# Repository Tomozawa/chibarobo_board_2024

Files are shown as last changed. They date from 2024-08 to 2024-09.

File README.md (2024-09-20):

# chiba_robo_board_2024
## 概要
ちばロボ2024に参加する1年生向けの制御基板です。

## 機能一覧
- マイコンボードESP32S2-DevKitM-1で操作可能
- Cytron MD10C向けコントロールピンx5
- 60kgサーボ向けコントロールピン&amp;7.5V/5A高効率電源
- マイコンボード直結GPIOピン
- 12~24VDC/50Aのアクチュエータ電源
- 外付け非常停止スイッチ
- ソフトスタート内蔵

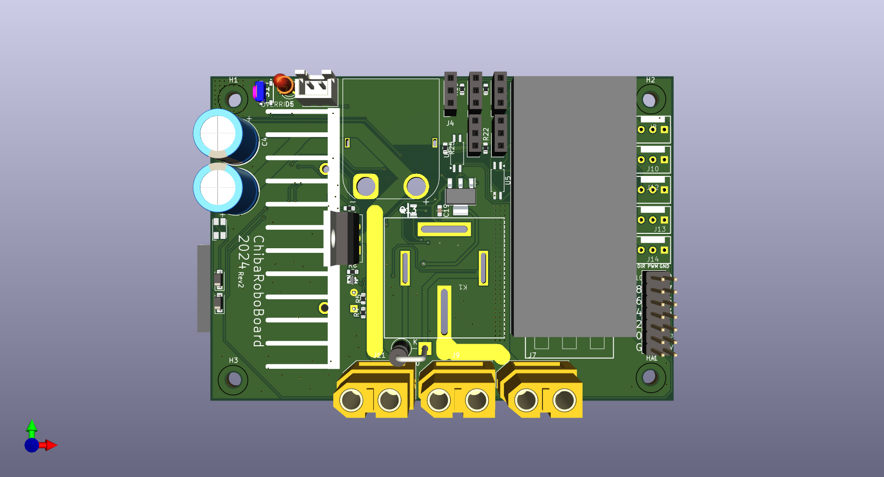
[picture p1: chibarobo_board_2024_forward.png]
chibarobo_board_2024_forward

<br>前面

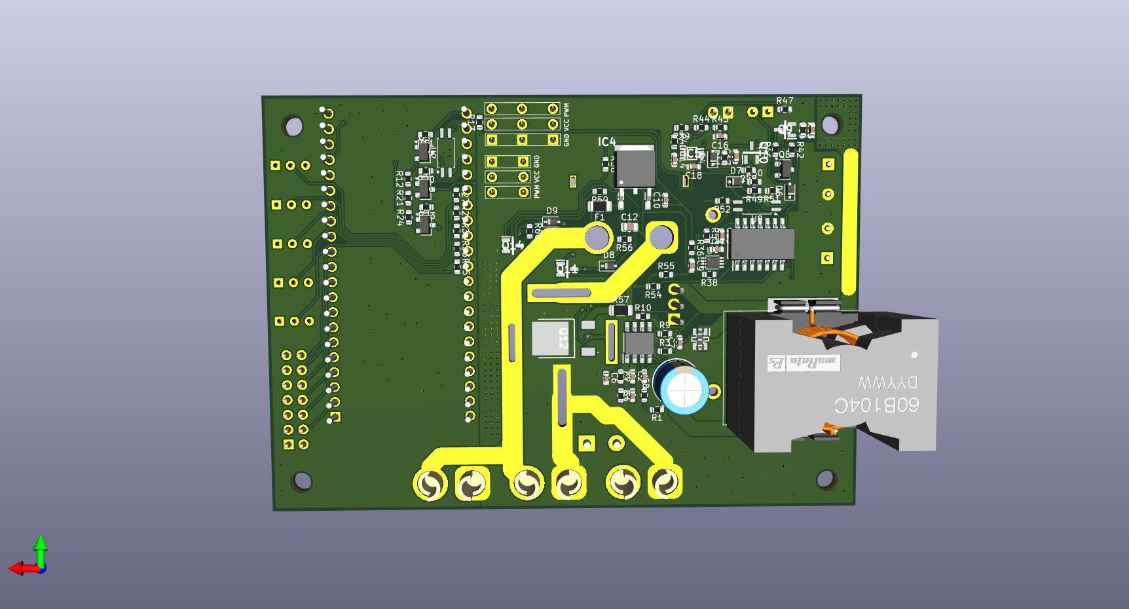
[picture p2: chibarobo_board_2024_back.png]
chibarobo_board_2024_back

<br>背面

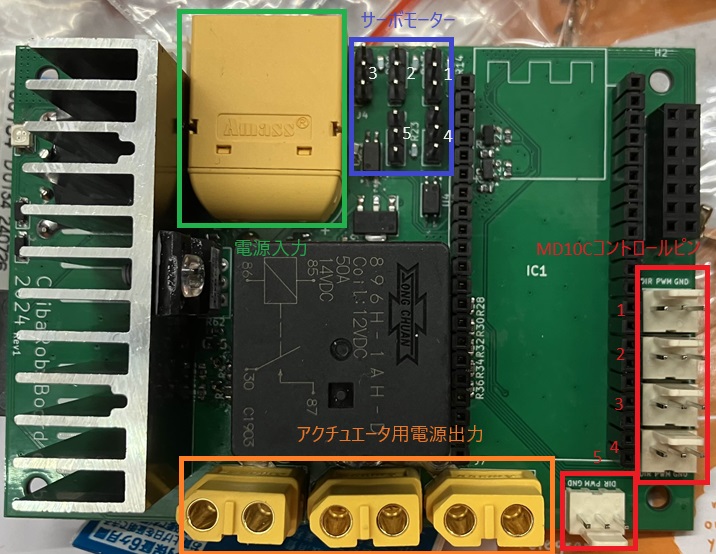
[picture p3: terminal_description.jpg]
terminal_descrition


# マイコンボード
本基板はESP32S2-DevKitM-1でアクチュエータ類を操作します。基板上のピンソケットに、シルクに描画されている向きに従ってESP32S2-DevKitM-1を差し込んでください。

各種アクチュエータ/センサとマイコンボードのピンアサインは以下のとおりです。
| ピン | アクチュエータ/センサ | 説明 |
| ----- | ----- | --- |
| 33 | DCモーター1 | DCモーター1のPWM信号 |
| 34 | DCモーター2 | DCモーター2のPWM信号 |
| 35 | DCモーター3 | DCモーター3のPWM信号 |
| 36 | DCモーター4 | DCモーター4のPWM信号 |
| 37 | DCモーター5 | DCモーター5のPWM信号 |
| 38 | DCモーター1 | DCモーター1のDIR信号 |
| 39 | DCモーター2 | DCモーター2のDIR信号 |
| 40 | DCモーター3 | DCモーター3のDIR信号 |
| 41 | DCモーター4 | DCモーター4のDIR信号 |
| 42 | DCモーター5 | DCモーター5のDIR信号 |
| 18 | サーボモーター1 | サーボモーター1のPWM信号 |
| 19 | サーボモーター2 | サーボモーター2のPWM信号 |
| 20 | サーボモーター3 | サーボモーター3のPWM信号 |
| 21 | サーボモーター4 | サーボモーター4のPWM信号 |
| 26 | サーボモーター5 | サーボモーター5のPWM信号 |
| 16 | 非常停止ボタン | HIGH: 非常停止ボタンが押されて**いない** LOW:非常停止ボタンが押されて**いる** |
| 5V || ロジック電源で動く回路の電源 |
| GND || ロジック電源で動く回路の共通電位 |

16番ピンは、出力モードに**設定しない**でください。非常停止ボタンのオーバーライド機能が無効になったり、非常停止ボタンが扱われた際、リレーが遮断しなくなることがあります。

# Cytron MD10C向けコントロールピン
Cytron製モータードライバ「Cytron MD10C」向けのDIR/PWM/GNDピンを5チャンネル提供します。

DIRピンのHigh/Low切り替えにより、回転方向を変化させます。

PWMピンから出力するPWM信号のデューティー比により、回転速度を変化させます。

GNDピンの電位は、マイコンボードのGNDピンと同電位です。

DIR/PWMピンの出力インピーダンスは2.2kOhm、ロジック電圧は3.3Vです。

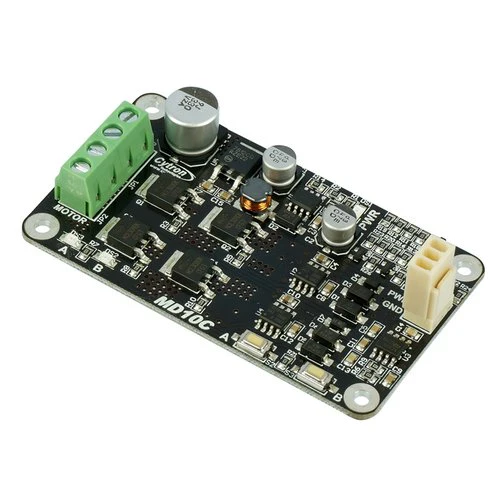
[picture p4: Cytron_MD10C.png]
Cytron MD10C


# サーボモーター電源/コントロールピン
60kgサーボ向けの7.5V/5A電源および、マイコンボードと絶縁されたPWM信号を提供します。

基板上のピンヘッダに、サーボモーターのQIコネクタを接続するだけで使用できます。

最大5個まで接続可能です(最小動作電流1Aの場合)。

> [!WARNING]
> - 3.3Vや5Vで動作するサーボモーターを接続しないでください。サーボモーターが焼損する可能性があります。
> - DCDCコンバータICの電流制限機能を外しています。出力電流の管理は、使用者の責任です(<span style="color: red;">最大5Aまで<span>)。

> [!NOTE]
> 無負荷時に150mA程度消費しますが、同期型DCDCコンバータの特性であり、故障ではありません。

# マイコンボード直結のGPIOピン
その他のアクチュエータおよびセンサを接続可能なGPIOピンを備えています。また、特定のGPIOピンからは、EMS信号(非常停止ボタンの信号)を取り出すことができます。(EMS信号を除き)出力電圧/電流は、ESP32S2-DevKitM-1の駆動能力に依存します。すなわち、3.3V/&pm;15mAの駆動能力を持ちます。

EMS信号は3.3V出力で、2.2kOhmの出力インピーダンスを持ちます。

# 12~24VDC/50Aのアクチュエータ電源
アクチュエータの動作に必要な電源を供給するための、電源ハブ機能を備えています。12~24VDC/50Aの範囲の直流電流を流すことができます。

# 外付け非常停止スイッチ
外付けの非常停止スイッチ(NO接点)を使うことで、非常時にアクチュエータ電源を遮断します。また、非常停止スイッチが扱われた際は、マイコンボードに信号が送られます。

外付け非常停止スイッチを使用しない場合、OVERRIDEボタンを使用することで、非常停止機能を一時的に無効にできます。

# ソフトスタート内蔵
バッテリーや端子への負荷を軽減するため、簡易的なソフトスタート機能を備えています。この機能は、電源投入から100ms間、アクチュエータ電源の消費電流を500mAに制限します。これは、アクチュエータ電源に2000uFまでの容量性負荷を接続することを可能にします。

# 確認されているバグ
- LEDのフットプリントミス(D0603サイズ(:サークル標準サイズ)のチップLEDを2つつけることで対処可能)

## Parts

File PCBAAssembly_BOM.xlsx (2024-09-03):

Designator | Comment | Footprint | JLCPCB Parts#
C1 | 8.2n | Capacitor_SMD:C_0603_1608Metric
C2 | 18p | Capacitor_SMD:C_0603_1608Metric
C3 | 3.3n | Capacitor_SMD:C_0603_1608Metric
C6 | 100n | Capacitor_SMD:C_0603_1608Metric
C7 | 100n | Capacitor_SMD:C_0603_1608Metric
C9 | 1u | Capacitor_SMD:C_0603_1608Metric
C10 | 100n | Capacitor_SMD:C_0603_1608Metric
C11 | 100n | Capacitor_SMD:C_0603_1608Metric
C12 | 10u | Capacitor_SMD:C_0805_2012Metric
C13 | 100n | Capacitor_SMD:C_0603_1608Metric
C14 | 100n | Capacitor_SMD:C_0603_1608Metric
C15 | 1u | Capacitor_SMD:C_0603_1608Metric
C16 | 100n | Capacitor_SMD:C_0603_1608Metric
C17 | 100n | Capacitor_SMD:C_0603_1608Metric
C18 | 100n | Capacitor_SMD:C_0603_1608Metric
D4 | D_Schottky | Diode_SMD:D_SOD-323F | C50704
D6 | D_Schottky | Diode_SMD:D_SOD-323F | C50704
D7 | D_Schottky | Diode_SMD:D_SOD-323F | C50704
D8 | 12V_Zener | Diode_SMD:D_SOD-323 | C19077447
D9 | 12V_Zener | Diode_SMD:D_SOD-323 | C19077447
IC4 | L78M05CDT | SamacSys_Parts:TO225P972X240-3N | C55509
Q3 | 2SA1162-GR_F_ | Package_TO_SOT_SMD:SC-59 | C155455
Q6 | 2SA1162-GR_F_ | Package_TO_SOT_SMD:SC-59 | C155455
Q7 | 2SA1162-GR_F_ | Package_TO_SOT_SMD:SC-59 | C155455
Q8 | 2SA1162-GR_F_ | Package_TO_SOT_SMD:SC-59 | C155455
Q9 | 2SC2712-GR_TE85L,F | SamacSys_Parts:SOT95P260X156-3N | C83447
Q10 | 2SC2712-GR_TE85L,F | SamacSys_Parts:SOT95P260X156-3N | C83447
Q11 | 2SC2712-GR_TE85L,F | SamacSys_Parts:SOT95P260X156-3N | C83447
Q14 | 2SC2712-GR_TE85L,F | SamacSys_Parts:SOT95P260X156-3N | C83447
R1 | 330 | Resistor_SMD:R_0603_1608Metric
R2 | 18 | Resistor_SMD:R_0603_1608Metric
R3 | 1.6k | Resistor_SMD:R_0603_1608Metric
R6 | 3k | Resistor_SMD:R_0603_1608Metric
R7 | 56k | Resistor_SMD:R_0603_1608Metric
R9 | 56k | Resistor_SMD:R_0603_1608Metric
R10 | 1k | Resistor_SMD:R_0603_1608Metric
R11 | 16k | Resistor_SMD:R_0603_1608Metric
R12 | 330 | Resistor_SMD:R_0603_1608Metric
R13 | 560 | Resistor_SMD:R_0603_1608Metric
R20 | 16k | Resistor_SMD:R_0603_1608Metric
R21 | 330 | Resistor_SMD:R_0603_1608Metric
R23 | 16k | Resistor_SMD:R_0603_1608Metric
R24 | 330 | Resistor_SMD:R_0603_1608Metric
R27 | 2.2k | Resistor_SMD:R_0603_1608Metric
R29 | 2.2k | Resistor_SMD:R_0603_1608Metric
R31 | 2.2k | Resistor_SMD:R_0603_1608Metric
R33 | 2.2k | Resistor_SMD:R_0603_1608Metric
R35 | 2.2k | Resistor_SMD:R_0603_1608Metric
R36 | 200k | Resistor_SMD:R_0603_1608Metric
R38 | 2.2k | Resistor_SMD:R_0603_1608Metric
R39 | 2.2k | Resistor_SMD:R_0603_1608Metric
R40 | 100k | Resistor_SMD:R_0603_1608Metric
R41 | 470 | Resistor_SMD:R_0603_1608Metric
R42 | 470 | Resistor_SMD:R_0603_1608Metric
R43 | 100 | Resistor_SMD:R_0603_1608Metric
R44 | 2.2k | Resistor_SMD:R_0603_1608Metric
R45 | 100k | Resistor_SMD:R_0603_1608Metric
R46 | 430 | Resistor_SMD:R_0603_1608Metric
R47 | 390 | Resistor_SMD:R_0603_1608Metric
R48 | 4.3k | Resistor_SMD:R_0603_1608Metric
R49 | 1.2k | Resistor_SMD:R_0603_1608Metric
R50 | 3.3k | Resistor_SMD:R_0603_1608Metric
R51 | 360 | Resistor_SMD:R_0603_1608Metric
R52 | 10k | Resistor_SMD:R_0603_1608Metric
R53 | 2.2k | Resistor_SMD:R_0603_1608Metric
R54 | 5.6k | Resistor_SMD:R_0603_1608Metric
R55 | 1k | Resistor_SMD:R_0603_1608Metric
R56 | 2.2k | Resistor_SMD:R_0603_1608Metric
R58 | 10k | Resistor_SMD:R_0603_1608Metric
R59 | 1.3k | Resistor_SMD:R_0603_1608Metric
R60 | 300 | Resistor_SMD:R_0603_1608Metric
U2 | TLP291 | Package_SO:SOIC-4_4.55x2.6mm_P1.27mm | C5121290
U7 | 74LVC1G123 | Package_SO:VSSOP-8_2.3x2mm_P0.5mm | C77273
U8 | TLP291 | Package_SO:SOIC-4_4.55x2.6mm_P1.27mm | C5121290

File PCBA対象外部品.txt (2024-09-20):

C4, C5, C19, C8, C19, D1, D2, D3, D5, D10, F1, HS1, IC1, IC2, IC3, IC5, J1, J8, J10, J12, J13, J14, K1, L1, Q1, Q12, Q13, Q15, Q2, Q4, Q5, R14, R15, R16, R17, R18, R19, R22, R25, R26, R28, R30, R32, R34, R37, R4, R5, R57, R8, S1, U1, U3, U4, U5, U6

所有(新品)
C4, C5, C19, F1, IC1, J8, J10, J12, J13, J14(1つのみ), K1, R28, R30, R32, R34, R37, R4, R5, S1

所有(部品取り)
D1(1つのみ), D2(1つのみ),D3(1つのみ), HS1(1つのみ), IC2(1つのみ), J8(1つのみ), J10(1つのみ), J12(1つのみ), J13(1つのみ), J14(1つのみ), L1(1つのみ), Q12(1つのみ), Q13, Q15(1つのみ), Q2(1つのみ), Q4, Q5, R57, R14, R15, R16, R17, R18, R19, R22, R25, R8, U3, U4, U5, U6

要購入
C8, D1(1つのみ), D2(1つのみ), D3(1つのみ), D5, D10, HS1(1つのみ), IC2(1つのみ), IC3, IC5, J1, L1(1つのみ), Q1, Q12(1つのみ), Q15(1つのみ), Q2(1つのみ), R57, U1

マルツ
D1(1つのみ), D2(1つのみ), D3(1つのみ), IC2(1つのみ), IC3, IC5, L1(1つのみ), Q1, Q12(1つのみ), Q15(1つのみ), Q2(1つのみ), R57, U1

秋月
C8, D10, J1

千石
D5, HS1(1つのみ),

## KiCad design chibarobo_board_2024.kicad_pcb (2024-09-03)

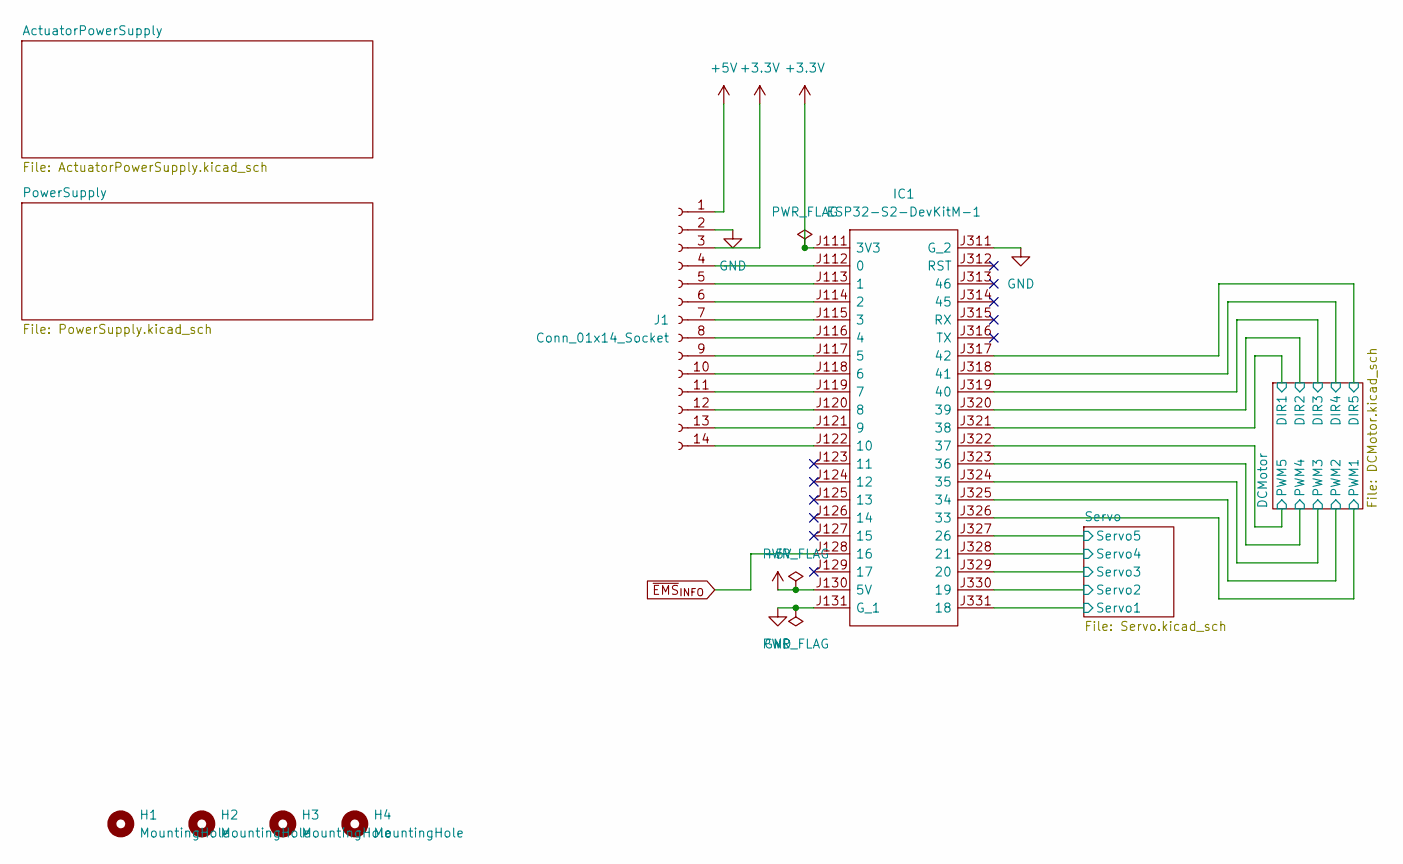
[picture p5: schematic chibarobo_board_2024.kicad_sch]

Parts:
H1, H2, H3, H4: MountingHole; MountingHole_3.2mm_M3
IC1: ESP32-S2-DevKitM-1; ESP32S2DevKitM1; Manufacturer_Part_Number ESP32-S2-DevKitM-1; Mouser Part Number 356-ESP32-S2DEVKITM1
J1: Conn_01x14_Socket; PinHeader_2x07_P2.54mm_Vertical

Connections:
+3.3V: IC1.J111 (3V3), J1.3
+5V: IC1.J130 (5V), J1.1; also elsewhere on the board
/DCMotor/DIR1: IC1.J321 (38); also elsewhere on the board
/DCMotor/DIR2: IC1.J320 (39); also elsewhere on the board
/DCMotor/DIR3: IC1.J319 (40); also elsewhere on the board
/DCMotor/DIR4: IC1.J318 (41); also elsewhere on the board
/DCMotor/DIR5: IC1.J317 (42); also elsewhere on the board
/DCMotor/PWM1: IC1.J326 (33); also elsewhere on the board
/DCMotor/PWM2: IC1.J325 (34); also elsewhere on the board
/DCMotor/PWM3: IC1.J324 (35); also elsewhere on the board
/DCMotor/PWM4: IC1.J323 (36); also elsewhere on the board
/DCMotor/PWM5: IC1.J322 (37); also elsewhere on the board
/Servo/Servo1: IC1.J331 (18); also elsewhere on the board
/Servo/Servo2: IC1.J330 (19); also elsewhere on the board
/Servo/Servo3: IC1.J329 (20); also elsewhere on the board
/Servo/Servo4: IC1.J328 (21); also elsewhere on the board
/Servo/Servo5: IC1.J327 (26); also elsewhere on the board
GND: IC1.J131 (G_1), IC1.J311 (G_2), J1.2; also elsewhere on the board
unnamed: IC1.J112 (0), J1.4
unnamed: IC1.J113 (1), J1.5
unnamed: IC1.J114 (2), J1.6
unnamed: IC1.J115 (3), J1.7
unnamed: IC1.J116 (4), J1.8
unnamed: IC1.J117 (5), J1.9
unnamed: IC1.J118 (6), J1.10
unnamed: IC1.J119 (7), J1.11
unnamed: IC1.J120 (8), J1.12
unnamed: IC1.J121 (9), J1.13
unnamed: IC1.J122 (10), J1.14
~EMS_{INFO}: IC1.J128 (16); also elsewhere on the board

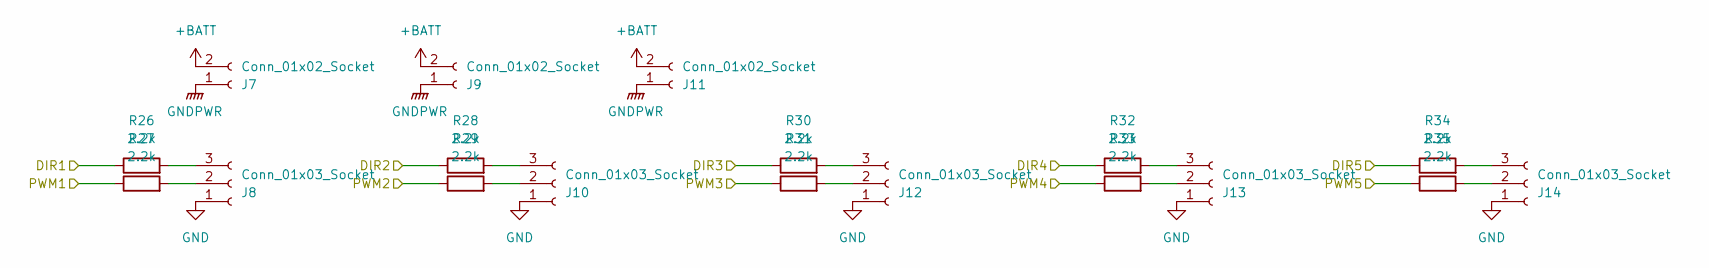
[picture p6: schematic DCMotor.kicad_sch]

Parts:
J7, J9, J11: Conn_01x02_Socket; AMASS_XT60-F_1x02_P7.20mm_Vertical
J8, J10, J12, J13, J14: Conn_01x03_Socket; Connector_2510-3P
R26, R27, R28, R29, R30, R31, R32, R33, R34, R35: 2.2k; R_0603_1608Metric

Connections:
+BATT: J7.2, J9.2, J11.2; also elsewhere on the board
/DCMotor/DIR1: R26.1; also elsewhere on the board
/DCMotor/DIR2: R28.1; also elsewhere on the board
/DCMotor/DIR3: R30.1; also elsewhere on the board
/DCMotor/DIR4: R32.1; also elsewhere on the board
/DCMotor/DIR5: R34.1; also elsewhere on the board
/DCMotor/PWM1: R27.1; also elsewhere on the board
/DCMotor/PWM2: R29.1; also elsewhere on the board
/DCMotor/PWM3: R31.1; also elsewhere on the board
/DCMotor/PWM4: R33.1; also elsewhere on the board
/DCMotor/PWM5: R35.1; also elsewhere on the board
GND: J8.1, J10.1, J12.1, J13.1, J14.1; also elsewhere on the board
GNDPWR: J7.1, J9.1, J11.1; also elsewhere on the board
unnamed: J8.2, R27.2
unnamed: J8.3, R26.2
unnamed: J10.2, R29.2
unnamed: J10.3, R28.2
unnamed: J12.2, R31.2
unnamed: J12.3, R30.2
unnamed: J13.2, R33.2
unnamed: J13.3, R32.2
unnamed: J14.2, R35.2
unnamed: J14.3, R34.2

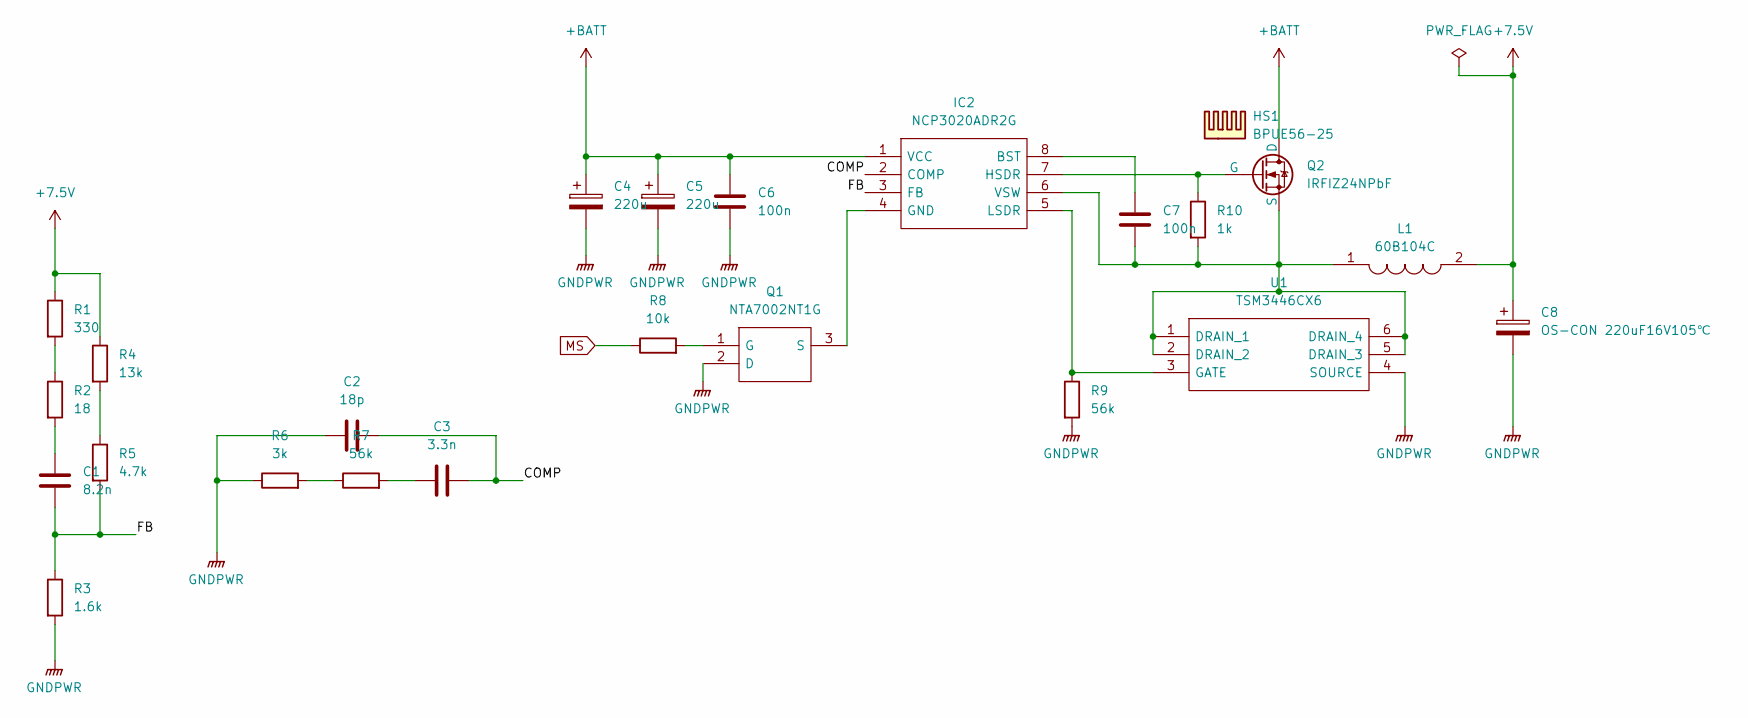
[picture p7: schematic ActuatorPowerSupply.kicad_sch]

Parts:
C1: 8.2n; C_0603_1608Metric
C2: 18p; C_0603_1608Metric
C3: 3.3n; C_0603_1608Metric
C4, C5: 220u; CP_Radial_D10.0mm_P5.00mm
C6, C7: 100n; C_0603_1608Metric
C8: OS-CON 220uF16V105℃; CP_Radial_D8.0mm_P3.50mm
HS1: BPUE56-25; BPUE56
IC2: NCP3020ADR2G; SOIC127P600X175-8N; Manufacturer_Part_Number NCP3020ADR2G; Mouser Part Number 863-NCP3020ADR2G
L1: 60B104C; 60B104C_correct; Manufacturer_Part_Number 60B104C; Mouser Part Number 580-60B104C
Q1: NTA7002NT1G; SOT50P160X90-3N; Manufacturer_Part_Number NTA7002NT1G; Mouser Part Number 863-NTA7002NT1G
Q2: IRFIZ24NPbF; TO-220-3_Vertical; JLCPCB Parts# C537925
R1: 330; R_0603_1608Metric
R2: 18; R_0603_1608Metric
R3: 1.6k; R_0603_1608Metric
R4: 13k; R_0603_1608Metric
R5: 4.7k; R_0603_1608Metric
R6: 3k; R_0603_1608Metric
R7, R9: 56k; R_0603_1608Metric
R8: 10k; R_0603_1608Metric
R10: 1k; R_0603_1608Metric
U1: TSM3446CX6; SOT95P280X95-6N; Manufacturer_Part_Number TSM3446CX6; Mouser Part Number 821-TSM3446CX6

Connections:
+7.5V: C8.1, L1.2, R1.1, R4.1; also elsewhere on the board
+BATT: C4.1, C5.1, C6.1, IC2.1 (VCC), Q2.2 (D); also elsewhere on the board
/ActuatorPowerSupply/COMP: C2.2, C3.2, IC2.2 (COMP)
/ActuatorPowerSupply/FB: C1.2, IC2.3 (FB), R3.1, R5.2
GNDPWR: C2.1, C4.2, C5.2, C6.2, C8.2, Q1.2 (D), R3.2, R6.1, R9.2, U1.4 (SOURCE); also elsewhere on the board
MS: R8.1; also elsewhere on the board
unnamed: C1.1, R2.2
unnamed: C3.1, R7.2
unnamed: C7.1, IC2.8 (BST)
unnamed: IC2.4 (GND), Q1.3 (S)
unnamed: IC2.7 (HSDR), Q2.1 (G), R10.1
unnamed: IC2.5 (LSDR), R9.1, U1.3 (GATE)
unnamed: C7.2, IC2.6 (VSW), L1.1, Q2.3 (S), R10.2, U1.1 (DRAIN_1), U1.2 (DRAIN_2), U1.5 (DRAIN_3), U1.6 (DRAIN_4)
unnamed: Q1.1 (G), R8.2
unnamed: R1.2, R2.1
unnamed: R4.2, R5.1
unnamed: R6.2, R7.1

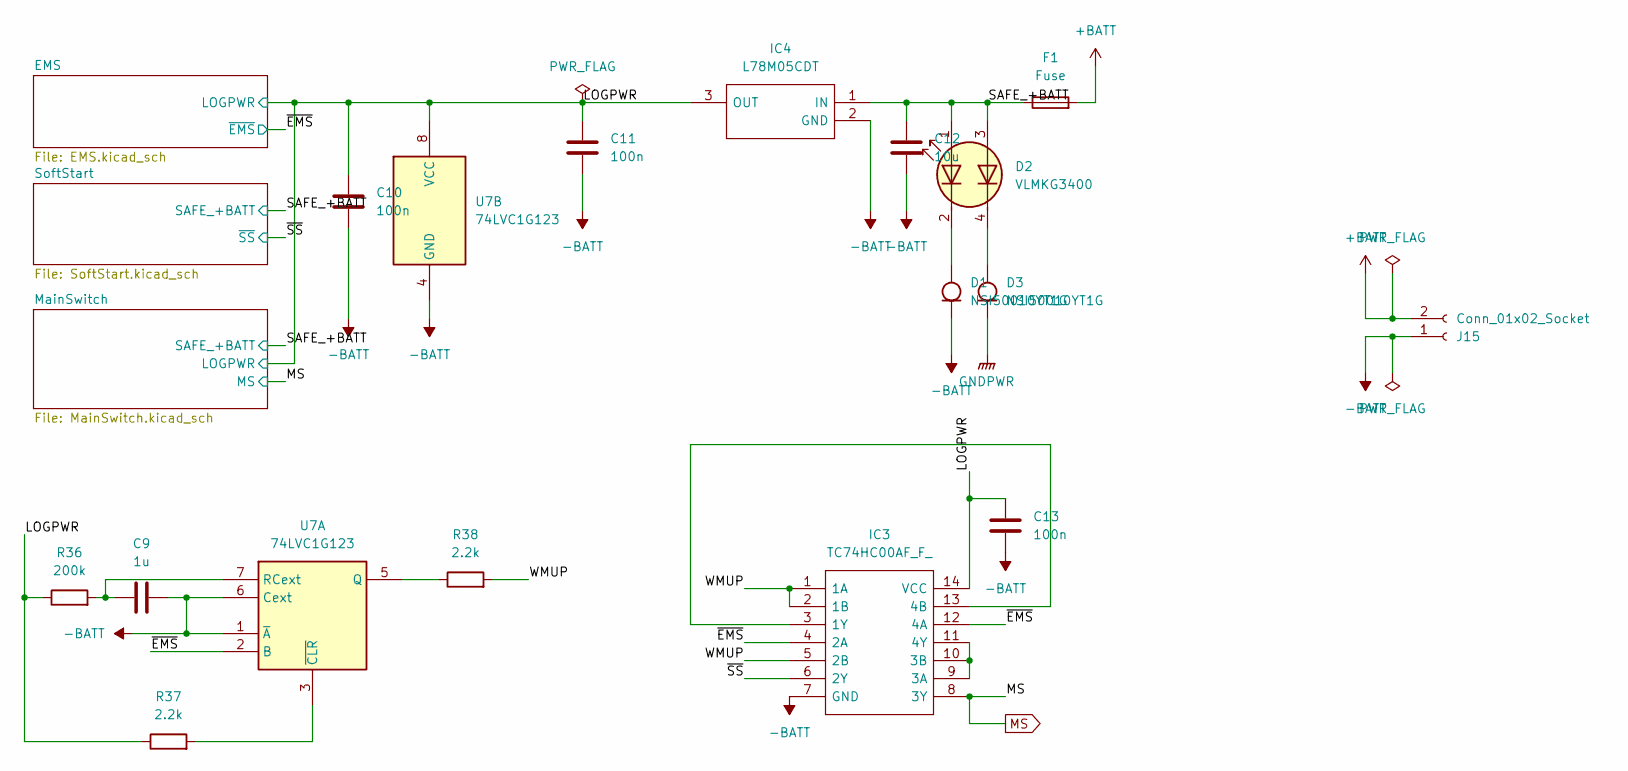
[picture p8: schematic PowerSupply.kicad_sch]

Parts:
C9: 1u; C_0603_1608Metric
C10, C11, C13: 100n; C_0603_1608Metric
C12: 10u; C_0805_2012Metric
D1, D3: NSI50010YT1G; D_SOD-123; JLCPCB Parts# C150049
D2: VLMKG3400; LED_Avago_PLCC4_3.2x2.8mm_CW; JLCPCB Parts# C5224081
F1: Fuse; Fuse_1206_3216Metric
IC3: TC74HC00AF_F_; SOIC127P780X190-14N; Manufacturer_Part_Number TC74HC00AF(F); JLCPCB Parts# C5381644
IC4: L78M05CDT; TO225P972X240-3N; Manufacturer_Part_Number L78M05CDT; Mouser Part Number 511-L78M05CDT
J15: Conn_01x02_Socket; AMASS_XT90PW-M_1x02_P11.00mm_Horizontal
R36: 200k; R_0603_1608Metric
R37, R38: 2.2k; R_0603_1608Metric
U7: 74LVC1G123; VSSOP-8_2.3x2mm_P0.5mm; JLCPCB Parts# C77273

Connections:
+BATT: F1.2, J15.2; also elsewhere on the board
-BATT: C9.2, C10.2, C11.2, C12.2, C13.2, D1.1 (K), IC3.7 (GND), IC4.2 (GND), J15.1, U7.1 (~A), U7.4 (GND), U7.6 (Cext); also elsewhere on the board
/PowerSupply/LOGPWR: C10.1, C11.1, C13.1, IC3.14 (VCC), IC4.3 (OUT), R36.1, R37.1, U7.8 (VCC); also elsewhere on the board
/PowerSupply/SAFE_+BATT: C12.1, D2.1 (AR), D2.3 (AG), F1.1, IC4.1 (IN); also elsewhere on the board
/PowerSupply/WMUP: IC3.1 (1A), IC3.2 (1B), IC3.5 (2B), R38.2
/PowerSupply/~EMS: IC3.4 (2A), IC3.12 (4A), U7.2 (B); also elsewhere on the board
/PowerSupply/~SS: IC3.6 (2Y); also elsewhere on the board
GNDPWR: D3.1 (K); also elsewhere on the board
MS: IC3.8 (3Y); also elsewhere on the board
unnamed: D1.2 (A), D2.2 (CR)
unnamed: D2.4 (CG), D3.2 (A)
unnamed: IC3.3 (1Y), IC3.13 (4B)
unnamed: IC3.9 (3A), IC3.10 (3B), IC3.11 (4Y)
unnamed: R38.1, U7.5 (Q)
unnamed: C9.1, R36.2, U7.7 (RCext)
unnamed: R37.2, U7.3 (~CLR)

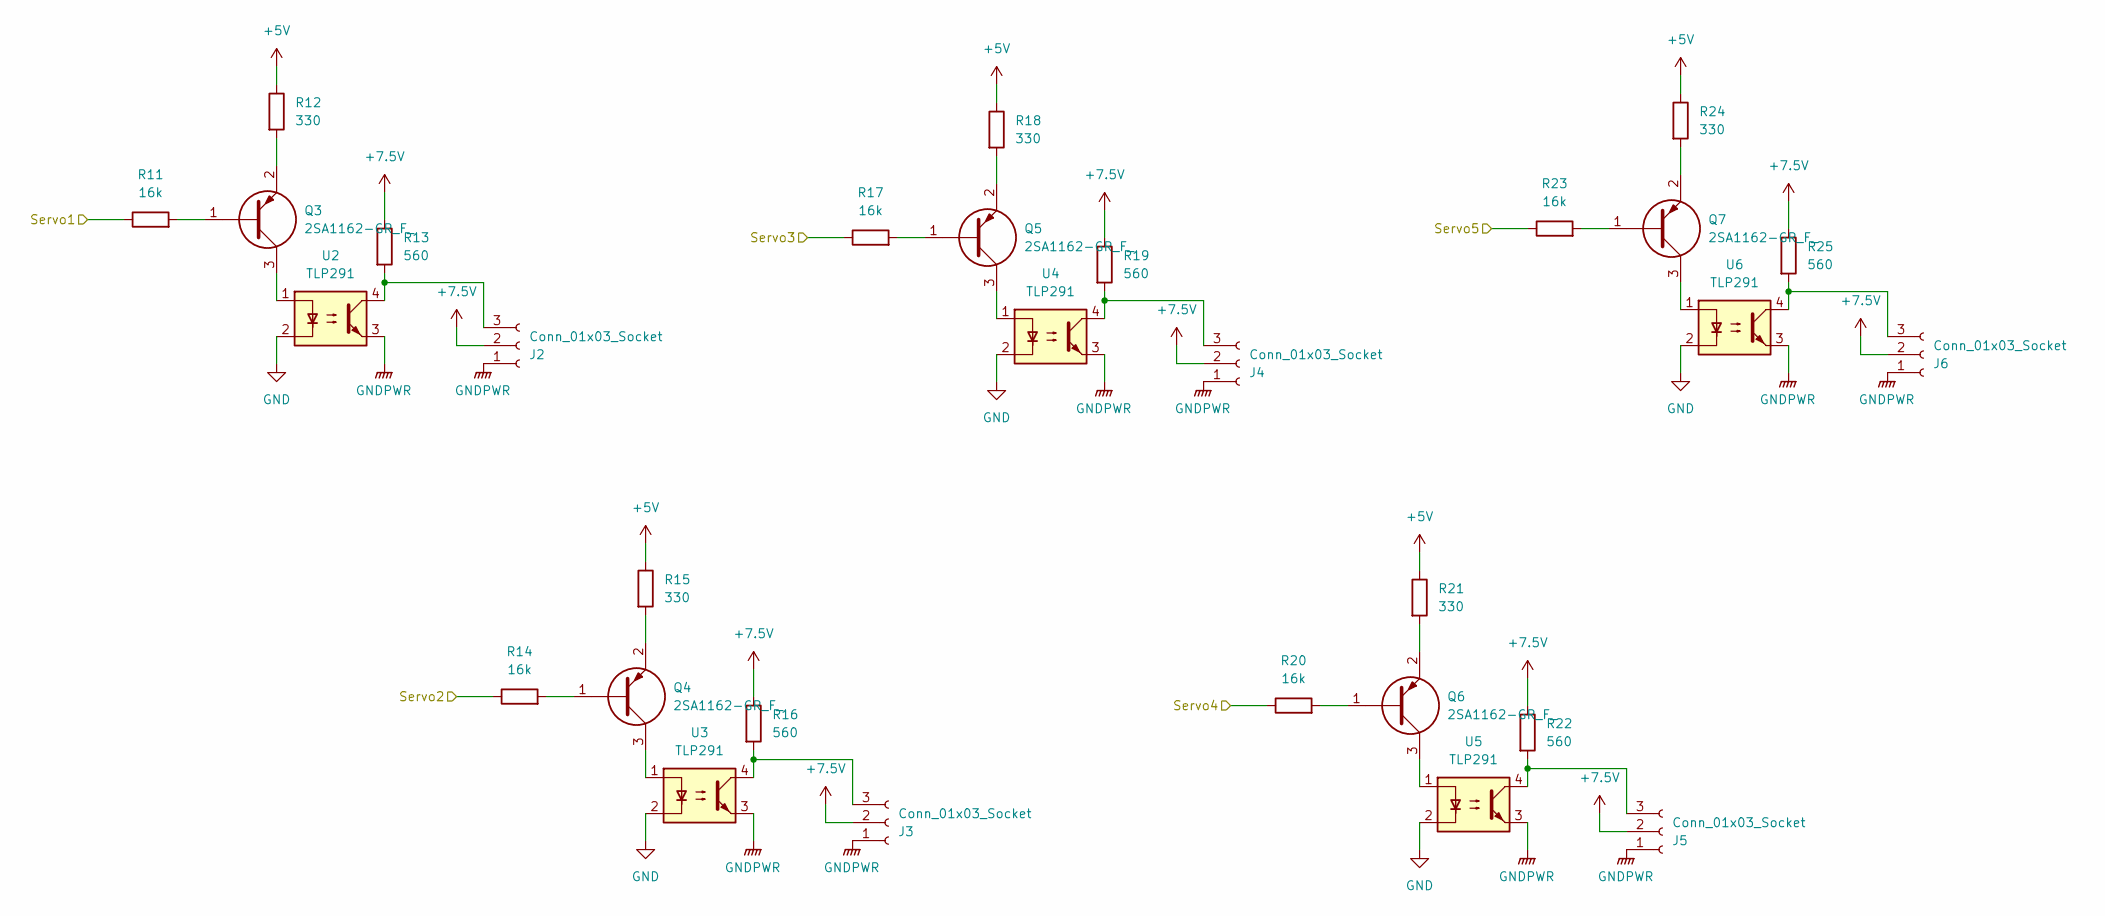
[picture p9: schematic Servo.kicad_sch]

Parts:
J2, J3, J4, J5, J6: Conn_01x03_Socket; PinSocket_1x03_P2.54mm_Vertical
Q3, Q4, Q5, Q6, Q7: 2SA1162-GR_F_; SC-59; Manufacturer_Part_Number 2SA1162-GR(F); JLCPCB Parts# C155455
R11, R14, R17, R20, R23: 16k; R_0603_1608Metric
R12, R15, R18, R21, R24: 330; R_0603_1608Metric
R13, R16, R19, R22, R25: 560; R_0603_1608Metric
U2, U3, U4, U5, U6: TLP291; SOIC-4_4.55x2.6mm_P1.27mm; JLCPCB Parts# C5121290

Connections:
+5V: R12.1, R15.1, R18.1, R21.1, R24.1; also elsewhere on the board
+7.5V: J2.2, J3.2, J4.2, J5.2, J6.2, R13.1, R16.1, R19.1, R22.1, R25.1; also elsewhere on the board
/Servo/Servo1: R11.1; also elsewhere on the board
/Servo/Servo2: R14.1; also elsewhere on the board
/Servo/Servo3: R17.1; also elsewhere on the board
/Servo/Servo4: R20.1; also elsewhere on the board
/Servo/Servo5: R23.1; also elsewhere on the board
GND: U2.2, U3.2, U4.2, U5.2, U6.2; also elsewhere on the board
GNDPWR: J2.1, J3.1, J4.1, J5.1, J6.1, U2.3, U3.3, U4.3, U5.3, U6.3; also elsewhere on the board
unnamed: J2.3, R13.2, U2.4
unnamed: J3.3, R16.2, U3.4
unnamed: J4.3, R19.2, U4.4
unnamed: J5.3, R22.2, U5.4
unnamed: J6.3, R25.2, U6.4
unnamed: Q3.1, R11.2
unnamed: Q3.2, R12.2
unnamed: Q3.3, U2.1
unnamed: Q4.1, R14.2
unnamed: Q4.2, R15.2
unnamed: Q4.3, U3.1
unnamed: Q5.1, R17.2
unnamed: Q5.2, R18.2
unnamed: Q5.3, U4.1
unnamed: Q6.1, R20.2
unnamed: Q6.2, R21.2
unnamed: Q6.3, U5.1
unnamed: Q7.1, R23.2
unnamed: Q7.2, R24.2
unnamed: Q7.3, U6.1

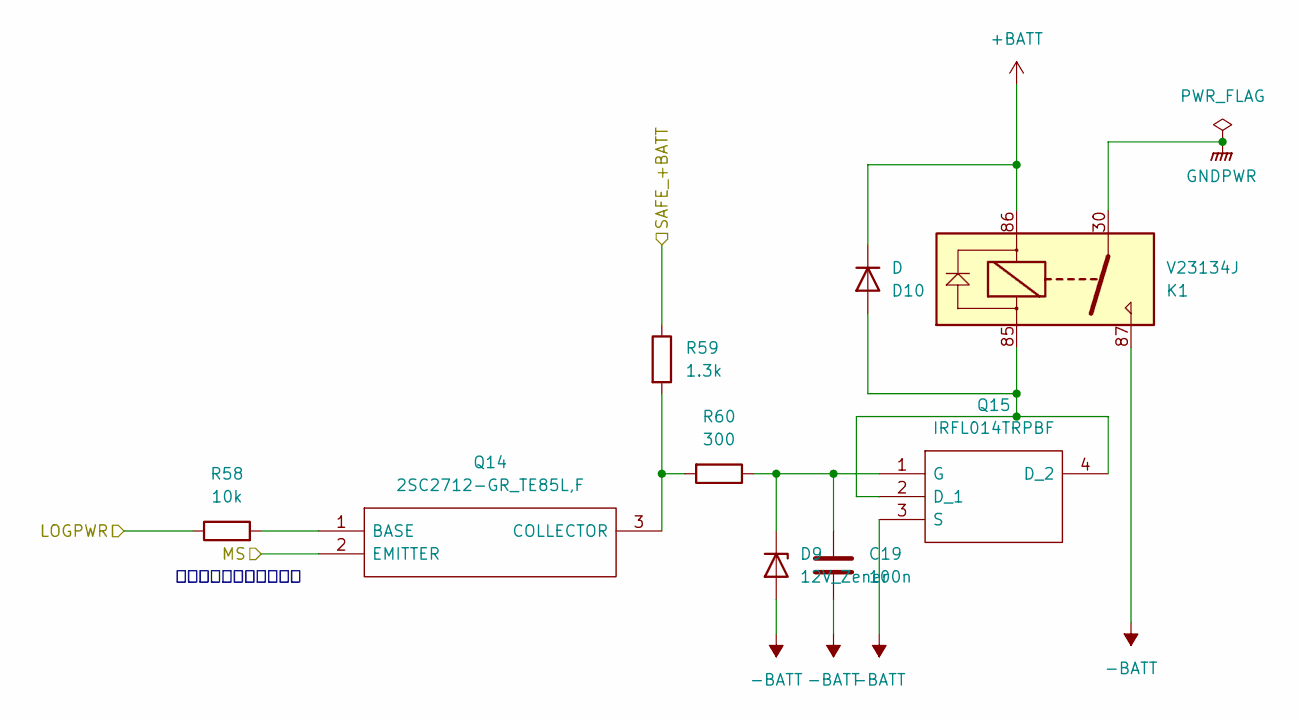
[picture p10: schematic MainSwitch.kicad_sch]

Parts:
C19: 100n; C_0603_1608Metric
D9: 12V_Zener; D_SOD-323; JLCPCB Parts# C19077447
D10: D; D_5W_P5.08mm_Vertical_KathodeUp
K1: V23134J; V23134J1052D642
Q14: 2SC2712-GR_TE85L,F; SOT95P260X156-3N; Manufacturer_Part_Number 2SC2712-GR(TE85L,F; Mouser Part Number 757-2SC2712-GRTE85LF
Q15: IRFL014TRPBF; SOT230P700X180-4N; Manufacturer_Part_Number IRFL014TRPBF; Mouser Part Number 844-IRFL014TRPBF
R58: 10k; R_0603_1608Metric
R59: 1.3k; R_0603_1608Metric
R60: 300; R_0603_1608Metric

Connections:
+BATT: D10.1 (K), K1.86; also elsewhere on the board
-BATT: C19.2, D9.2 (A), K1.87, Q15.3 (S); also elsewhere on the board
/PowerSupply/LOGPWR: R58.1; also elsewhere on the board
/PowerSupply/SAFE_+BATT: R59.1; also elsewhere on the board
GNDPWR: K1.30; also elsewhere on the board
MS: Q14.2 (EMITTER); also elsewhere on the board
unnamed: C19.1, D9.1 (K), Q15.1 (G), R60.1
unnamed: D10.2 (A), K1.85, Q15.2 (D_1), Q15.4 (D_2)
unnamed: Q14.1 (BASE), R58.2
unnamed: Q14.3 (COLLECTOR), R59.2, R60.2

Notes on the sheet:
シンク駆動ができること

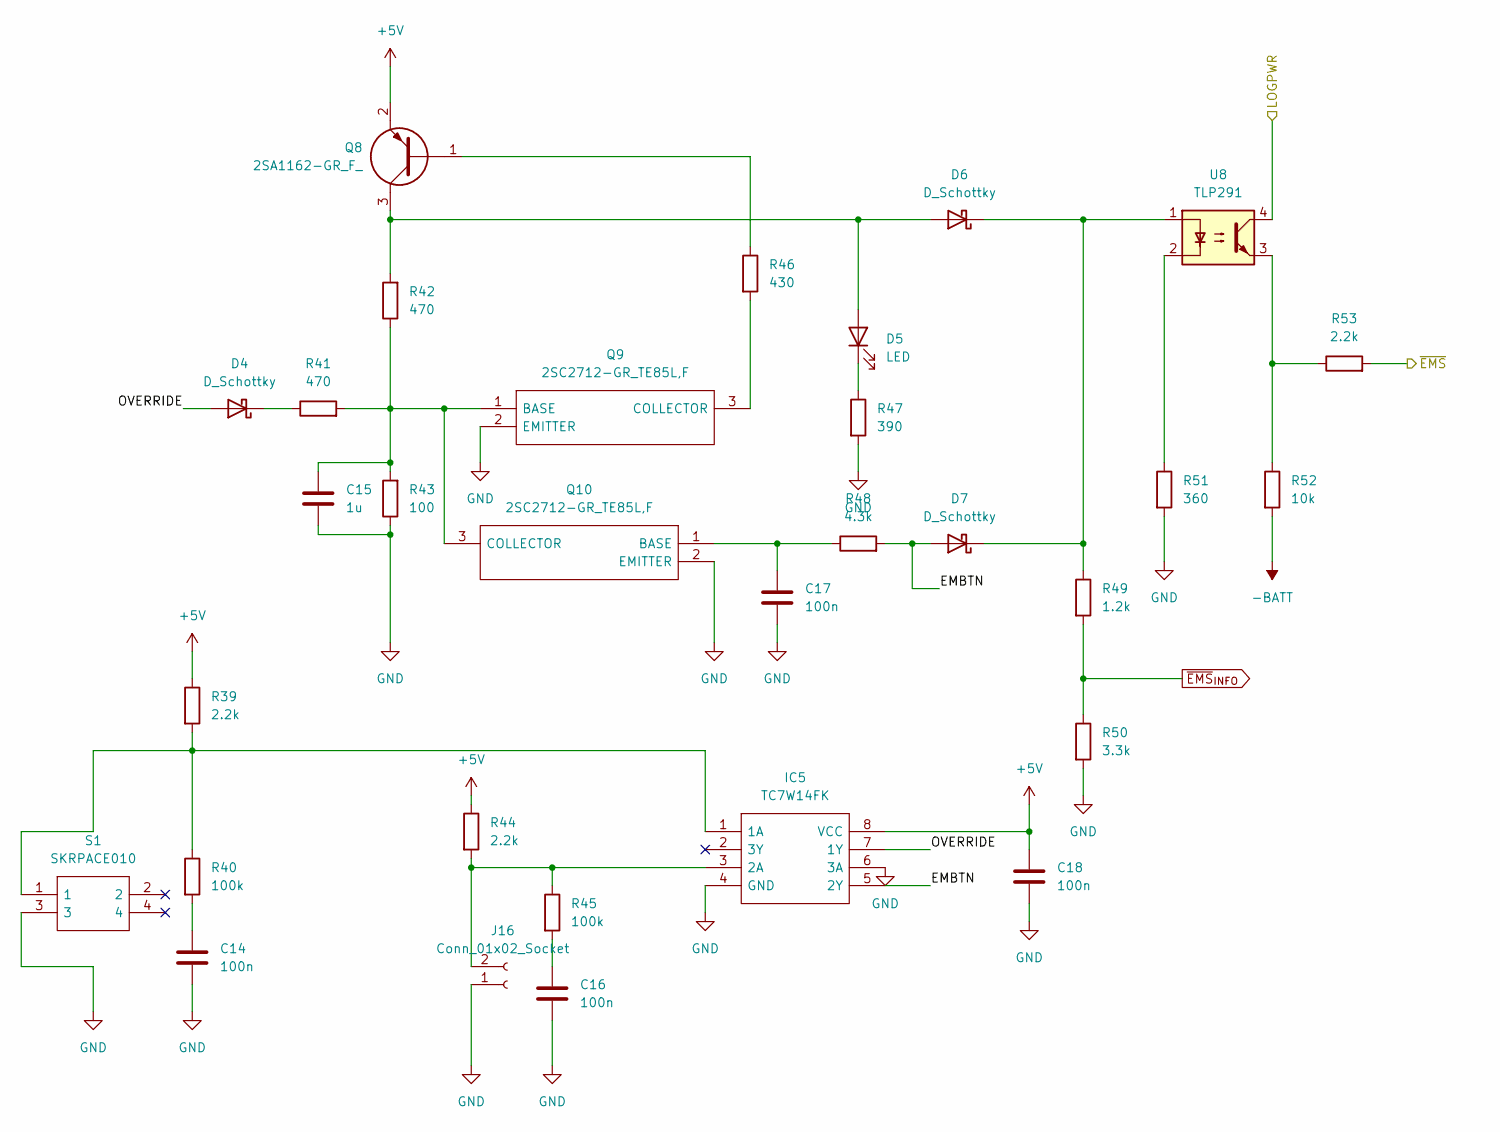
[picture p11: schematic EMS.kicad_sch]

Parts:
C14, C16, C17, C18: 100n; C_0603_1608Metric
C15: 1u; C_0603_1608Metric
D4, D6, D7: D_Schottky; D_SOD-323F; JLCPCB Parts# C50704
D5: LED; LED_D3.0mm
IC5: TC7W14FK; SOP50P310X90-8N; Manufacturer_Part_Number TC7W14FK; JLCPCB Parts# C5156512
J16: Conn_01x02_Socket; JST_XH_B2B-XH-A_1x02_P2.50mm_Vertical
Q8: 2SA1162-GR_F_; SC-59; Manufacturer_Part_Number 2SA1162-GR(F); JLCPCB Parts# C155455
Q9, Q10: 2SC2712-GR_TE85L,F; SOT95P260X156-3N; Manufacturer_Part_Number 2SC2712-GR(TE85L,F; Mouser Part Number 757-2SC2712-GRTE85LF
R39, R44, R53: 2.2k; R_0603_1608Metric
R40, R45: 100k; R_0603_1608Metric
R41, R42: 470; R_0603_1608Metric
R43: 100; R_0603_1608Metric
R46: 430; R_0603_1608Metric
R47: 390; R_0603_1608Metric
R48: 4.3k; R_0603_1608Metric
R49: 1.2k; R_0603_1608Metric
R50: 3.3k; R_0603_1608Metric
R51: 360; R_0603_1608Metric
R52: 10k; R_0603_1608Metric
S1: SKRPACE010; SMT_4.2X3.2_; Manufacturer_Part_Number SKRPACE010; Mouser Part Number 688-SKRPACE010
U8: TLP291; SOIC-4_4.55x2.6mm_P1.27mm; JLCPCB Parts# C5121290

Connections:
+5V: C18.1, IC5.8 (VCC), Q8.2, R39.1, R44.1; also elsewhere on the board
-BATT: R52.2; also elsewhere on the board
/PowerSupply/EMS/EMBTN: D7.2 (A), IC5.5 (2Y), R48.2
/PowerSupply/EMS/OVERRIDE: D4.2 (A), IC5.7 (1Y)
/PowerSupply/LOGPWR: U8.4; also elsewhere on the board
/PowerSupply/~EMS: R53.2; also elsewhere on the board
GND: C14.2, C15.2, C16.2, C17.2, C18.2, IC5.4 (GND), IC5.6 (3A), J16.1, Q9.2 (EMITTER), Q10.2 (EMITTER), R43.1, R47.2, R50.2, R51.2, S1.3; also elsewhere on the board
unnamed: C14.1, R40.2
unnamed: C16.1, R45.2
unnamed: D4.1 (K), R41.1
unnamed: D5.2 (A), D6.2 (A), Q8.3, R42.2
unnamed: D5.1 (K), R47.1
unnamed: D6.1 (K), D7.1 (K), R49.1, U8.1
unnamed: IC5.1 (1A), R39.2, R40.1, S1.1
unnamed: IC5.3 (2A), J16.2, R44.2, R45.1
unnamed: Q8.1, R46.1
unnamed: Q9.3 (COLLECTOR), R46.2
unnamed: C17.1, Q10.1 (BASE), R48.1
unnamed: C15.1, Q9.1 (BASE), Q10.3 (COLLECTOR), R41.2, R42.1, R43.2
unnamed: R51.1, U8.2
unnamed: R52.1, R53.1, U8.3
~EMS_{INFO}: R49.2, R50.1; also elsewhere on the board

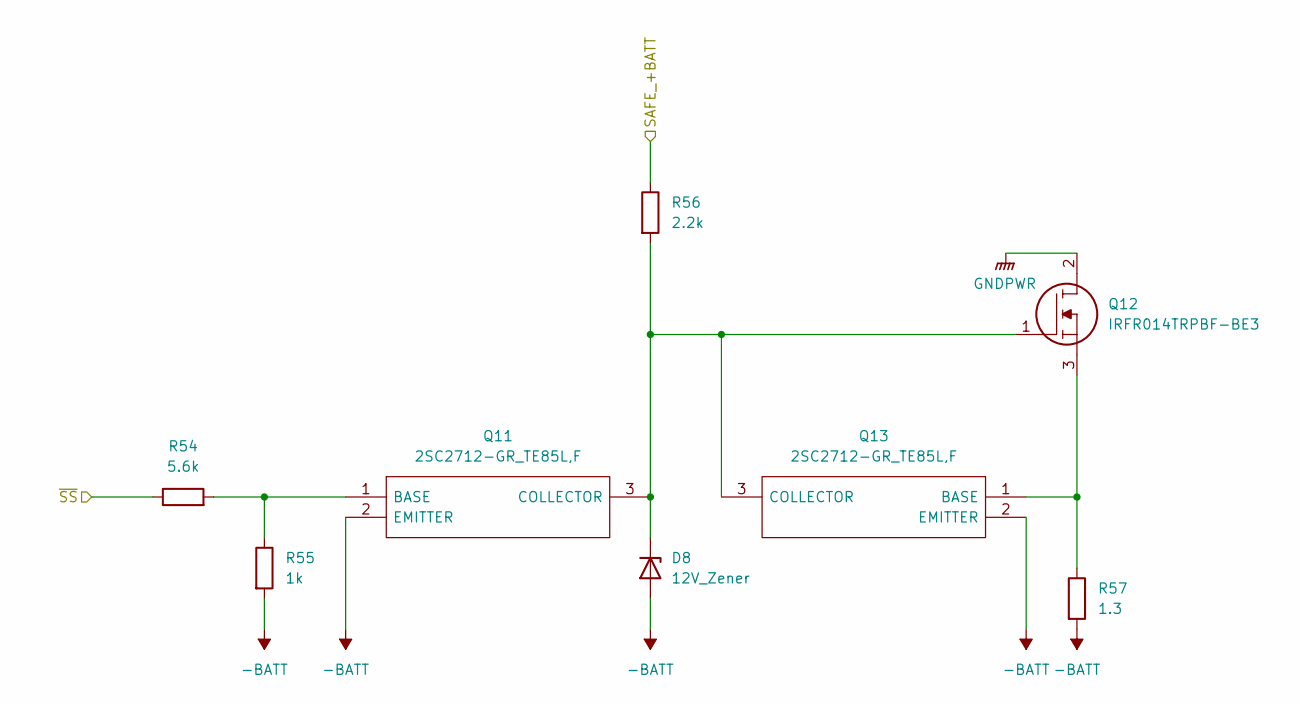
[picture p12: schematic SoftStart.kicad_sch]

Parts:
D8: 12V_Zener; D_SOD-323; JLCPCB Parts# C19077447
Q11, Q13: 2SC2712-GR_TE85L,F; SOT95P260X156-3N; Manufacturer_Part_Number 2SC2712-GR(TE85L,F; Mouser Part Number 757-2SC2712-GRTE85LF
Q12: IRFR014TRPBF-BE3; IRFR014TRPBFBE3; Manufacturer_Part_Number IRFR014TRPBF-BE3; Mouser Part Number 78-IRFR014TRPBF-BE3
R54: 5.6k; R_0603_1608Metric
R55: 1k; R_0603_1608Metric
R56: 2.2k; R_0603_1608Metric
R57: 1.3; R_1206_3216Metric; JLCPCB Parts# C4048845

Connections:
-BATT: D8.2 (A), Q11.2 (EMITTER), Q13.2 (EMITTER), R55.2, R57.2; also elsewhere on the board
/PowerSupply/SAFE_+BATT: R56.1; also elsewhere on the board
/PowerSupply/~SS: R54.1; also elsewhere on the board
GNDPWR: Q12.2; also elsewhere on the board
unnamed: D8.1 (K), Q11.3 (COLLECTOR), Q12.1, Q13.3 (COLLECTOR), R56.2
unnamed: Q11.1 (BASE), R54.2, R55.1
unnamed: Q12.3, Q13.1 (BASE), R57.1

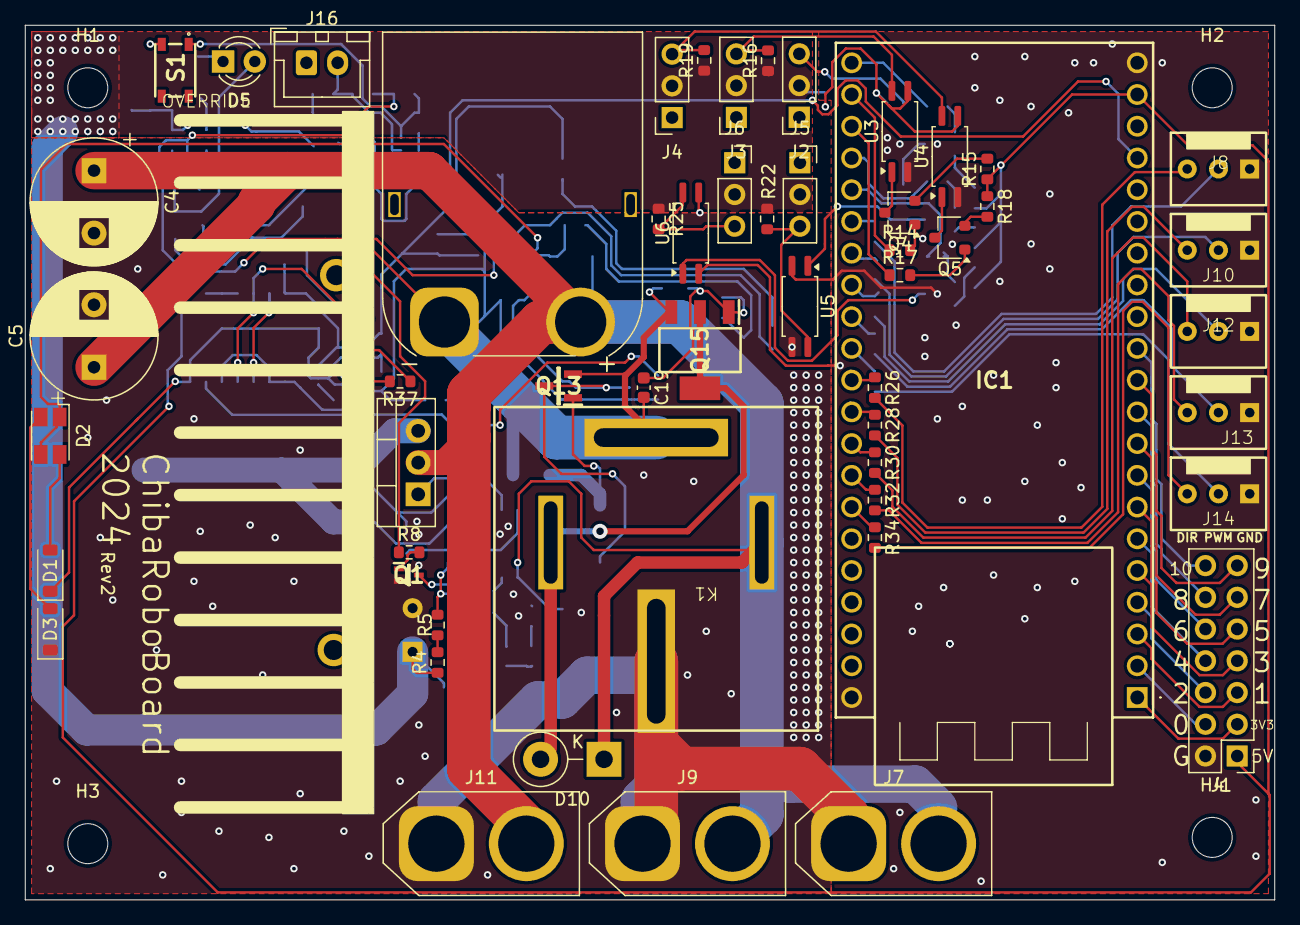
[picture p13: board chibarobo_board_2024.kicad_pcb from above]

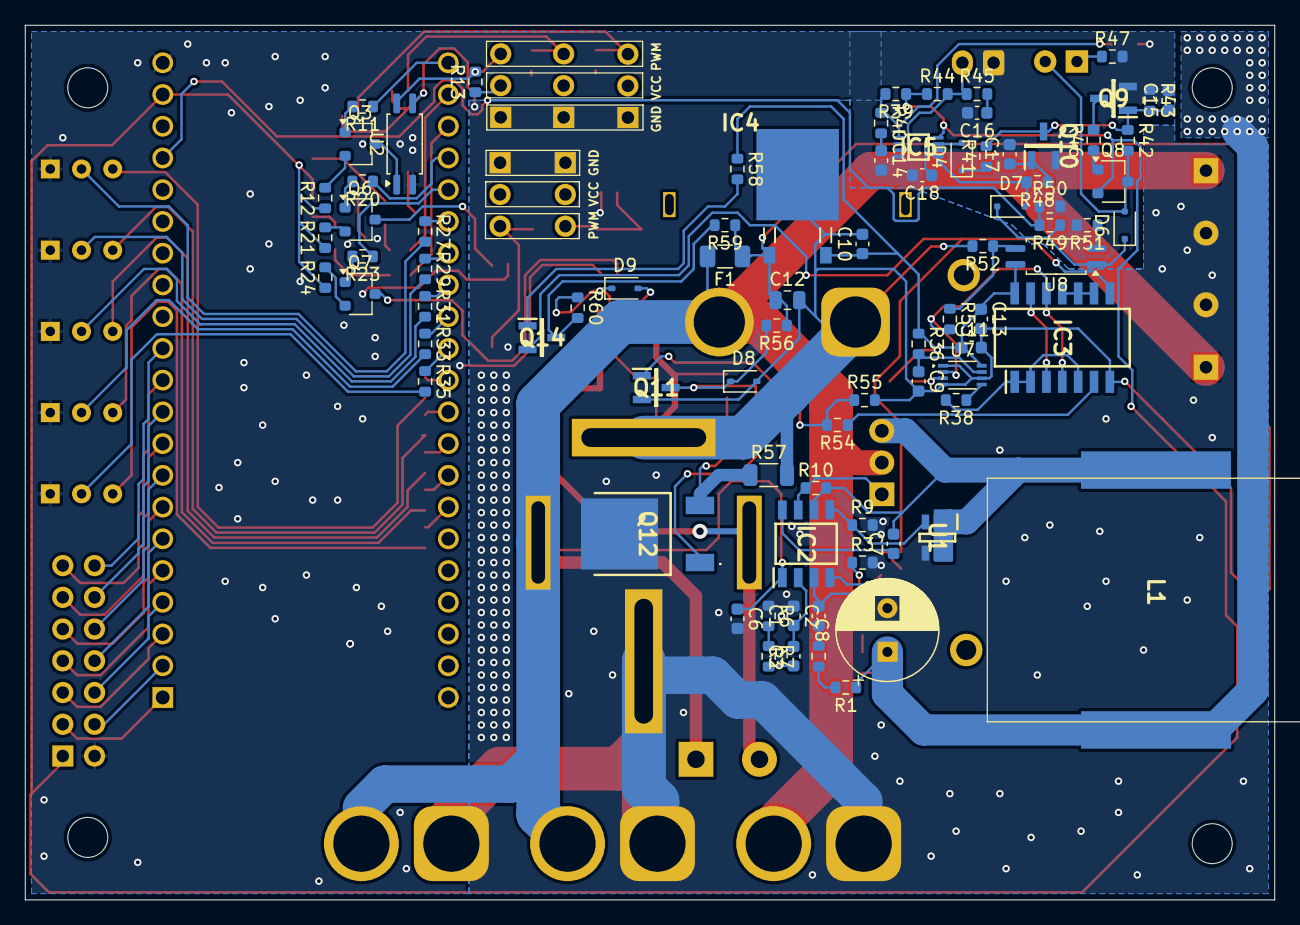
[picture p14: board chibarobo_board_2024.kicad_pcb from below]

Board: 2 copper layers, 100.0 x 70.0 mm, 142 parts (83 on the bottom side), 113 nets.

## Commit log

2024-08-29 Recalculate OTA feedback
    [OTA補償回路定数計算.xlsx]
2024-08-31 before elimination of J7
    [ActuatorPowerSupply.kicad_sch, DCMotor.kicad_sch, EMS.kicad_sch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]
2024-09-03 add order information
    [PCBAAssembly_BOM.xlsx, SoftStart.kicad_sch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]
